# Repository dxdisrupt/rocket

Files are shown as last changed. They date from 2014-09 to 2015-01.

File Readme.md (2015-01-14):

<a name="Title" />
# Compressed Air Rocket and Spark Core Setup #

<a name="overview" />
## Overview ##

The compressed air rocket used here is based on the one presented by Make Magazine in **[How-to: Building a compressed air rocket launcher] (http://makezine.com/2010/07/11/how-to-building-the-compressed-air/)**

You can make your own rockets using a legal sheet of paper, some napkins (to add support to the nose cone), and copious amounts of tape.  Get the template here: [Rocket_Template.pdf](Rocket_Template.pdf?raw=true)

There is an alternate set of instructions for the rocket launcher with more complete instructions on creating the paper rockets here: http://cdn.makezine.com/make/2010/04/compressedairrocket.pdf .  A copy of the PDF is also included in this repository here: [compressedairrocket.pdf](compressedairrocket.pdf?raw=true)

---

<a name="BuildInfo" />
## Build Your Own ##

These docs were originally written to help somebody configure the rocket launcher that was shipped to them.  However, there is only one in existence right now so if you wait to have it shipped to you, you may be waiting a while, and you can't keep it for long.  

Building one is not hard, is great to do with kids or really any group.  

1. Follow the instructions to create your own rocket launcher:
	- [How-to: Building a compressed air rocket launcher] (http://makezine.com/2010/07/11/how-to-building-the-compressed-air/) 
	- Alternate instructions: [compressedairrocket.pdf](compressedairrocket.pdf?raw=true)
	- PDF Template for Paper Rockets: [Rocket_Template.pdf](Rocket_Template.pdf?raw=true)

1. Get a [Spark Core](https://www.spark.io/store) (The one with the chip attenna is fine for most use cases.  If you will be using this outside far away from your WiFi hotspot, you may prefer the one with the ufl connector so you can attach an external antenna for extended range. 

1. Get a Spark Core [Relay Shield](https://www.spark.io/store) 

1. Additional misc parts:

	- Project enclosure for the Spark Relay Sheild, Spark Core, and 9V Battery (I used a sandwich container from the dollar store! High class huh!)

	- Optional On/Off switch for the Spark Core (to help save the battery when you aren't using it)

	- Wire to connect the Spark Core

- An Adventerous attitude is required.  You will likely need to "invent" a few things as you build your own system.  If I get to where I can spec out exact parts and process I will, but then that would take some of the fun out of building your own version. 

---

<a name="inventory" />
## Inventory ##

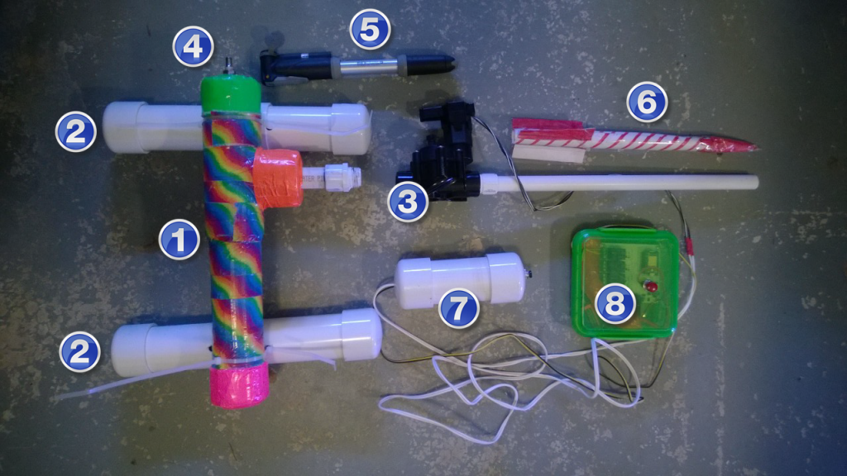
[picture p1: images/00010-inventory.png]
00010-Inventory Inventory


1. Compression Chamber
2. Feet - Attached with Zip Ties
3. Springer Valve and Launch Tube
4. Shrader Valve to charge compression chamber
5. Bike Pump - Attaches to Shrader Valve
6. Paper & Tape Rocket
7. Manual Firing Button & 9v Power Supply
8. Spark Core & Relay Board

The following schematic gives you the basics of the eletronics although the schematic isn't exact.  It was built in [Fritzing](fritizing.org) and there is not current a fritzing part for the Spark IO Relay Shield, so the connections have been approximated here:

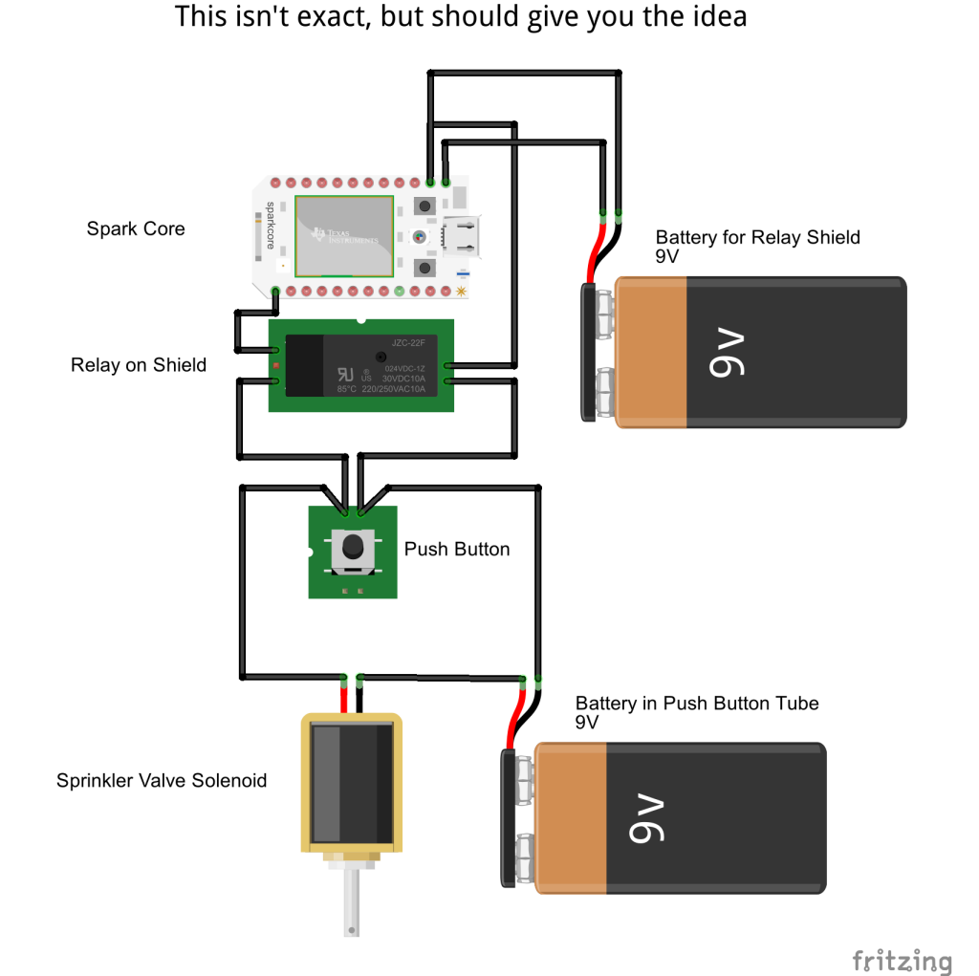
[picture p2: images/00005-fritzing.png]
00005-Fritzing Fritzing


--- 

<a name="tasks" />
## Tasks  ##

1. [Assembling the Rocket Launcher](#Task1)
1. [Installing the Spark Core Windows USB Driver](#Task2)
1. [Installing the Spark-CLI](#Task3)
1. [Configuring WiFi for a Pre-Programmed Spark Core](#Task4)
1. [Flashing the relayWidget Sketch](#Task5)
1. [Identifying your Spark Core](#Task6)
1. [Testing the Spark Core](#Task7)
1. [Using Visual Studio to Create a Launcher Web Site](#Task8)
1. [Publishing your Web Site to Azure](#Task9)

---

<a name="Task1" />
## Assembling the Rocket Launcher ##

1.  Attach the **Sprinkler Valve and Launch Tube** (3) to the **Compression Chamber** (1) using the using the threaded PVC tubing extending from the compression chamber and threading it into the bottom of the sprinkler valve. 

	> **Note:** Be sure that you have it threaded on tightly.  If need be use some plumbers tape to help ensure a good seal.  If the seal here is not good, air will leak out. 

1.  Attach the **Compression Chamber** (1) to the **Feet** (2) using .zip ties.  Tighten the zip ties enough to hold the compression chamber in place, but loose enough that you can still tilt the launch tube for aiming purposes. 

1. **CAREFULLY** remove the cap with the button on it from the **"Manual Firing Button and 9v Power Supply"** by twisting it back and forth while pulling it away from the tube. 

	> **Note:** If you are using my rocket, I just improved the connections inside the tube so you don't have to be AS CAREFUL, but you don't want to the yank the cap off and break the connections.

1. Inside the tube, you should find the 9V Battery and the 9V battery connector.  Connect the battery to the snap connector, then re-insert the battery in the tube and replace the cap. 

	> **Note:** The 9V battery in the push button tube is what actually supplies the power for the sprinkler valve solenoid.  If you make sure to only have the battery connected when you are actively using the rocket, it should last for a very long time.  If you find that the Solenoid does not open when you push the button, you may try replacing the 9V battery in the tube. 

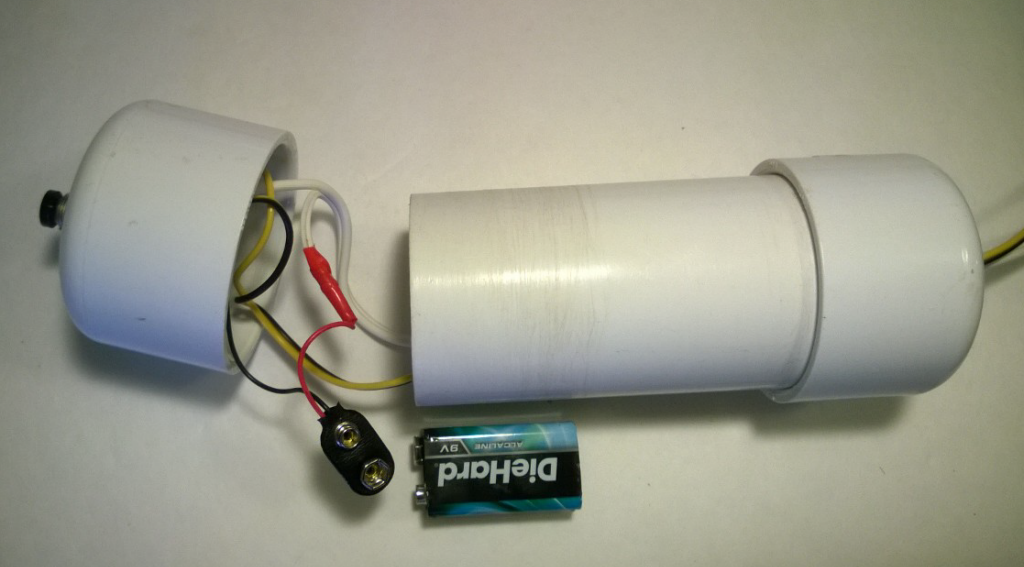
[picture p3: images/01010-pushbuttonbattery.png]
01010-PushButtonBattery Push Button Battery
	

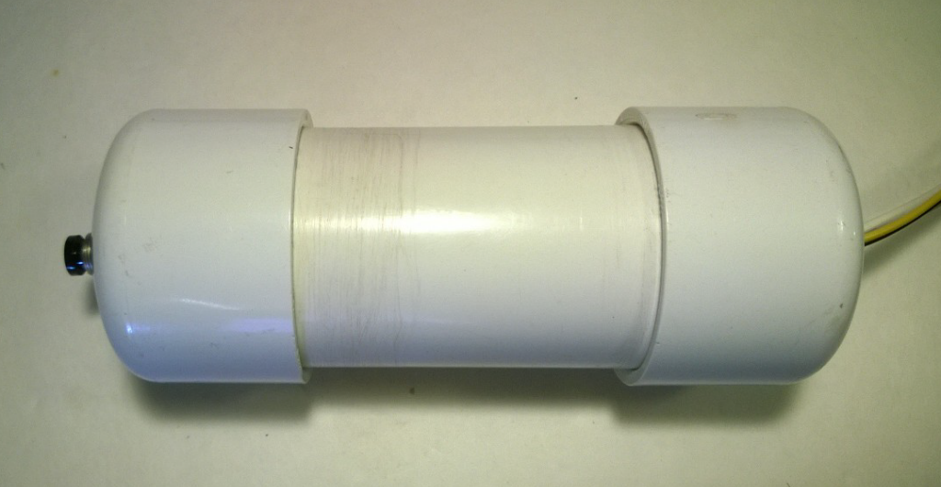
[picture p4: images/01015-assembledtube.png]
01015-AssembledTube Assembled Tube
	

1. I added some disconnects between the sprinkler valve and the manual push button and spark core relay board assemblies.  This makes it easier to disconnect them for shipping.

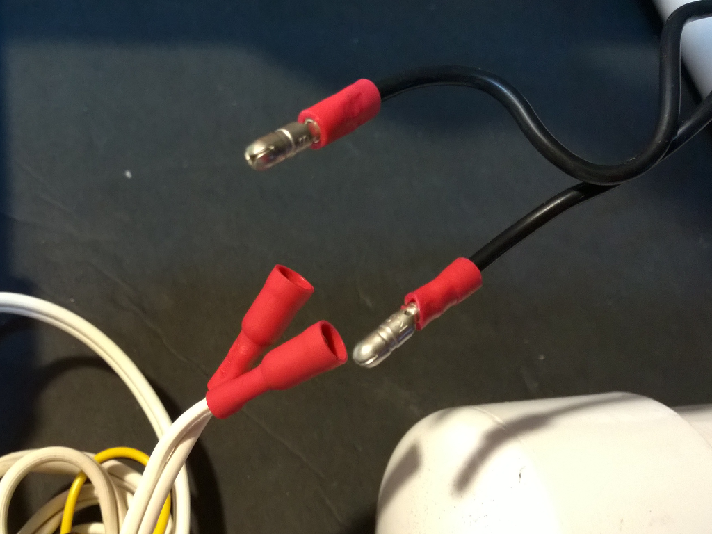
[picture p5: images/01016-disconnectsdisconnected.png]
01016-DisconnectsDisconnected Disconnects Disconnected
	

1. Simply re-connect them if they are disconnected.  ***It doesn't matter which black wire connects to which white wire.  Either way is fine.*** 

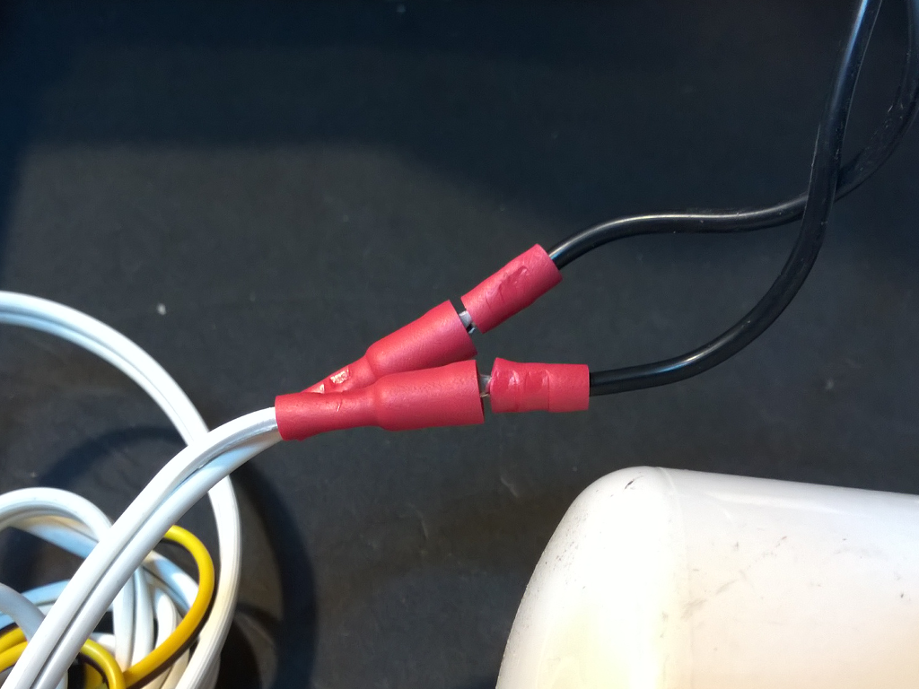
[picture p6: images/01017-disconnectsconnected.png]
01017-DisconnectsConnected Disconnects Connected
	

1. You should now be able to push the pushbutton and hear the solenoid on the sprinkler valve opening and closing (faintly).  If you hold your hand on the solendoid while you repeatedly push the button, you should also be able to feel the solenoid opening and closing. 

1. Attach the **Bike Pump** (5) to the **Shrader Valve** (4).  Again, ensure a good connection. 

1. You can now pump the bycicle pump (just a few times for this initial test): 
	- **WITHOUT A ROCKET** on the launch tube
	- Make sure to **STAY CLEAR OF THE LAUNCH TUBE**

1. **When you know it is safe to do so**, push the manual push button, and verify that air is released from the launch tube.  **Hold the push button down for five seconds to allow all of the air to escape.** 

1. Assuming everything has worked so far, if you have a rocket handy, and you just can't wait, go ahead and **SAFELY** try firing a rocket.  Remember, this is supposed to be a fun thing, not a weapon.  Please **DO NOT EVER AIM THE ROCKET AT SOMEBODY**. I have had MULTIPLE accidental misfires during my use of the rocket, and have been very lucky to have never injured anybody, but this can be dangerous, so please take care. 

	You can aim the rocket by rotating the compression chamber.  If the zip ties are too loose you can tighten them up to add enough friction to keep the compression chamber in place after "aiming"

1. Here is the final assembled rocket launcher:

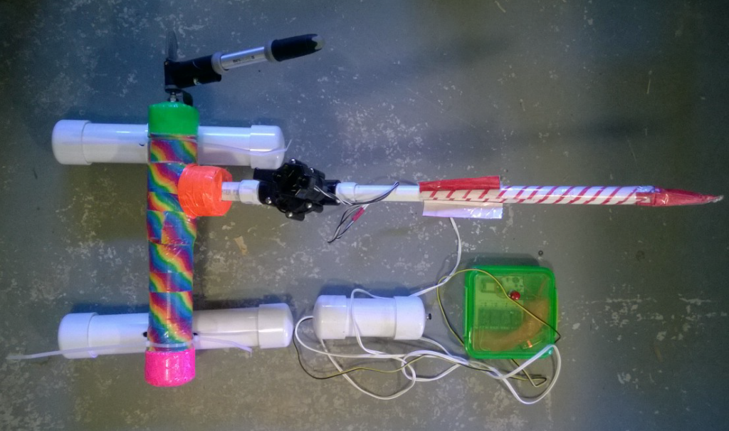
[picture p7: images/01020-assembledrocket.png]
01020-AssembledRocket Assembled Rocket
	

---

<a name="Task2" />
## Installing the Spark Core Windows USB Driver ##

### <span style="color: #090">IF YOU ALREADY HAVE THE WINDOWS USB DRIVER INSTALLED YOU CAN SKIP THIS TASK</span> ###

The steps covered here are specific to configuring a Spark Core using the Command Line Interface on a Windows machine. If you will be working with the spark core from a Mac or Linux box, you can can refer to the [online documentation](http://docs.spark.io/ "Spark.IO Documentation") for configuring a Spark Core. 

1. Before you work with the Spark Core on a Windows Machine, you will need to install the Windows USB Driver.  First, you'll need to download the driver from https://s3.amazonaws.com/spark-website/Spark.zip . Download the .zip file and extract it to a folder on your computer.  

	> **Note:** You can also refer to the documentation for [Connecting to the Spark Core via USB](http://docs.spark.io/connect/#connecting-your-core-connect-over-usb)

1. Connect the Spark Core to your computer via the USB, and ensure that the Spark Core is in **["Listening Mode"](http://docs.spark.io/connect/#connecting-your-core-listening-mode)** by confirming that the RGB LED on the board is flashing blue.  If it isn't, [hold the **"MODE"** button on the Spark Core for about three seconds until it begins flashing](https://vine.co/v/hFHlpBDELeU):

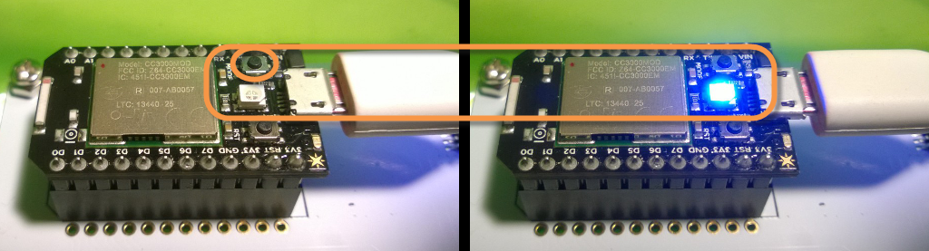
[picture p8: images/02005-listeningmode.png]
02005-ListeningMode Listening Mode
	

1. Open your computer's **"Device Manager"**.  Under **"Other Devices"** you should see the **"Spark Core with WiFi"**.  Right click on the **"Spark Core with WiFi"** and select **"Update Driver Software..."** from the pop-up menu: 

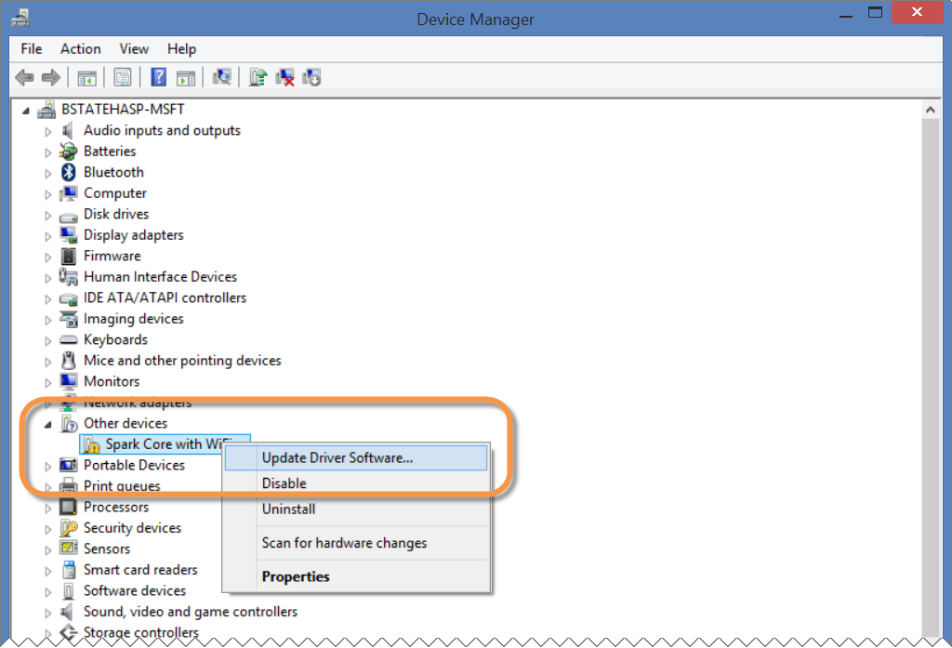
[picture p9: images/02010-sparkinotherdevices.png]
02010-SparkInOtherDevices Spark in Other Devices
	

1. Select the **"Browse my computer for driver software"** option:

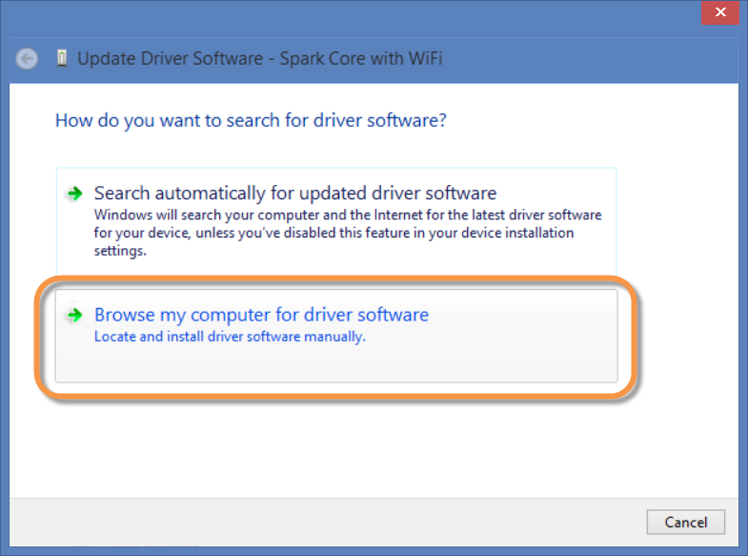
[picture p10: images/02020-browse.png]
02020-Browse Browse
	

1. Then browse to the folder where you extracted the Spark.zip file you downloaded previously with the Windows USB driver.  (There should be a **spark_core.inf** and **spark_core.cat** file in the folder), then click **"Next"**:

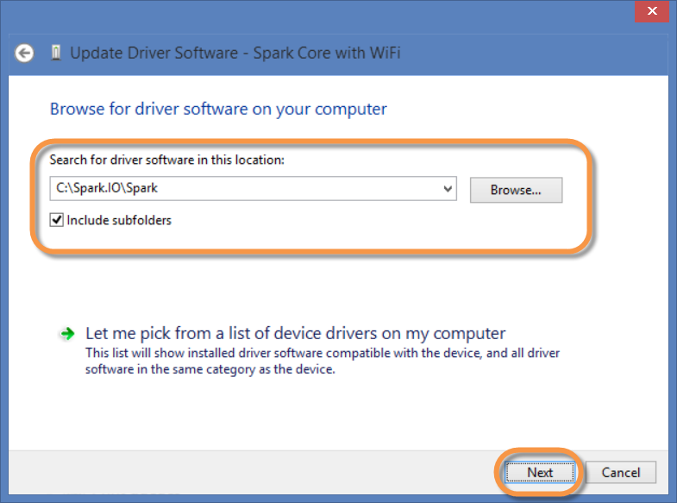
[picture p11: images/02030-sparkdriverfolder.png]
02030-SparkDriverFolder Spark Driver Folder
	

1. In the **"Windows Security"** window, click **"Install"** to install the driver:

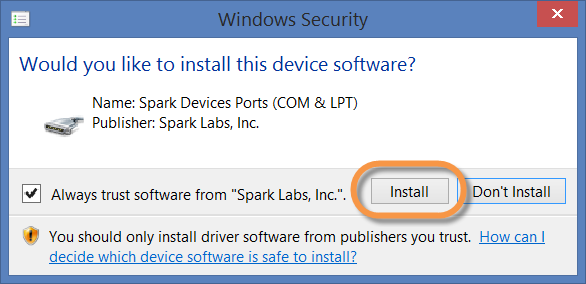
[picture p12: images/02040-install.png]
02040-Install Install
	

1. You should see a confirmation that the **"Spark Core with Wifi and Arduino Compatability"** driver was installed.  Click **"Close"** to close the window. 

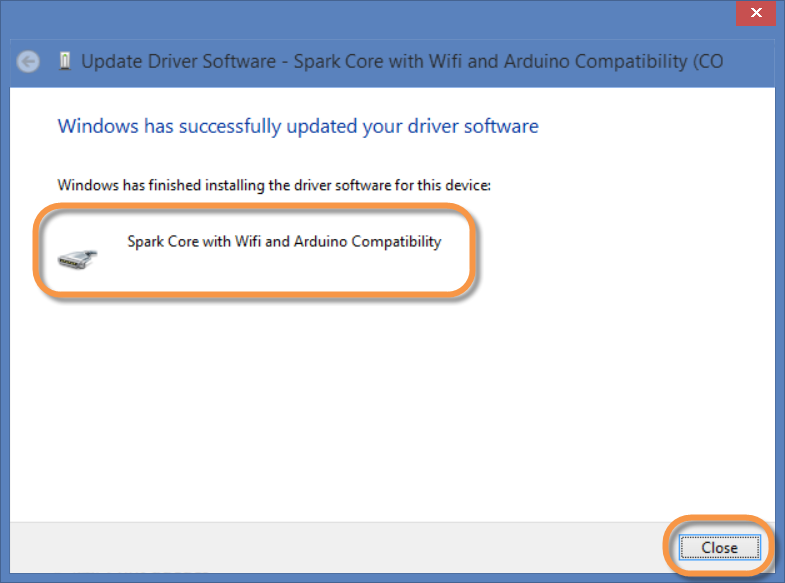
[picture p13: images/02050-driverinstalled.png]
02050-DriverInstalled Driver Installed
	

1. Finally, back in the **"Device Manager"** you should see the Spark Core listed under **"Ports"**:

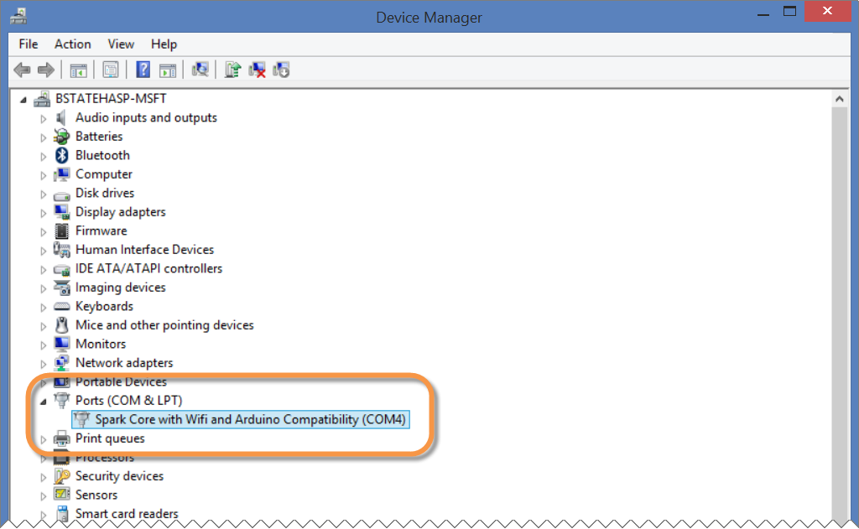
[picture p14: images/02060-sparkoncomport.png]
02060-SparkOnComPort Spark Core on COM Port
	

1. At this point, if you were to use a terminal program (Like [PuTTY](http://www.chiark.greenend.org.uk/~sgtatham/putty/download.html)) you could connect serially to the Spark Core via the COM port listed (COM4 in this case) and issue [some commands](http://docs.spark.io/connect/#connecting-your-core-connect-over-usb).  However, the Spark Command Line Interface (Spark-CLI) offers significantly more functionality, so we'll use that.  

---

<a name="Task3" />
## Installing the Spark-CLI ##

### <span style="color: #090">IF YOU ALREADY HAVE THE LATEST VERSION OF THE SPARK-CLI INSTALLED YOU CAN SKIP THIS TASK</span> ###

The S**park Command Line Interface (Spark-CLI)** is a **Node.js** application that allows you to manage your spark cores, and the code that runs on them.  The Spark-CLI source is available from GitHub at https://github.com/spark/spark-cli and you can read the docs here: http://docs.spark.io/cli/

1.  First, ensure that you have Node.js installed.  You can install it from here: http://nodejs.org/

	> **Note:** It helps if you let the installer install the Node Package Manager (npm) as well as to add Node to the system path.  If you add node the path, you can use node from any Windows Command Prompt. 

1. To install the Spark-CLI using node, you can open a Node.js Command Prompt (or any command administrator prompt if you allowed the Node.js installer to add Node to the path) and issue the following command:

	`npm install -g spark-cli`

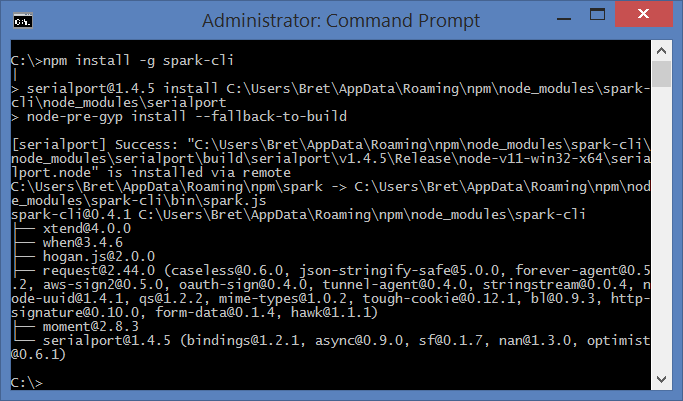
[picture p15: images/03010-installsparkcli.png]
03010-InstallSparkCLI Install Spark-CLI
	

1. This documentation was written with the Spark-CLI version 0.4.1.  If you already have the Spark-CLI installed, you can determine its version using the following command:

	`npm list -g spark-cli`

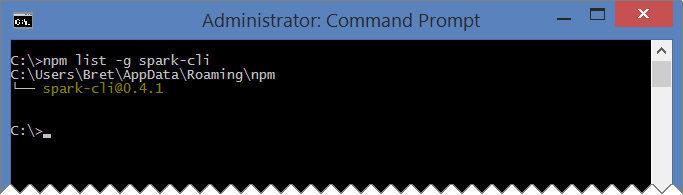
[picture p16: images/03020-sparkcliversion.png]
03020-SparkCliVersion SparkCliVersion
	

1. In addition, you can always upgrade to the latest version of the Spark-CLI using the command: 

	`npm update -g spark-cli`

---

<a name="Task4" />
## Configuring WiFi for a Pre-Programmed Spark Core ##

### <span style="color: #900; font-weight: bold">IF YOU ARE ADDING YOUR OWN SPARK CORE, OR NEED TO RE-PROGRAM AN EXISTING SPARK CORE, SKIP THIS STEP AND GO TO [Flashing the relayWidget Sketch](#Task5)</span> ###

If you received the rocket launcher, with a Spark Core that has been pre-programmed, a Relay Board, and everything already connected, you only need to configure the Spark Core to connect to your local WiFi.

1. Connect the Spark Core to your PC via USB, and place the Spark Core into **"[Listening Mode](http://docs.spark.io/connect/#connecting-your-core-listening-mode)"** by holding down the **"Mode"** button on the spark core until the RGB LED flashes blue repeatedly.

1. Open a Node Command Prompt, and issue the following command 

	`spark setup wifi`

1. Follow the prompts to configure the Spark Core for your WiFi network.  

	> **Note:** Some MiFi wifi hot sports (like my Verizon MiFi), and other networks take the user to a start screen on the first load.  If connecting to your mifi, the Spark might fail to connect the first time.  Try cycling the power on your Spark Core to get it to restart and connect.  If the WiFi network you are connecting to requires a browser based authentication process, you won't be able to connect your Spark Core to it.  You must know the WiFi SSID, Security Mode, and Password.  

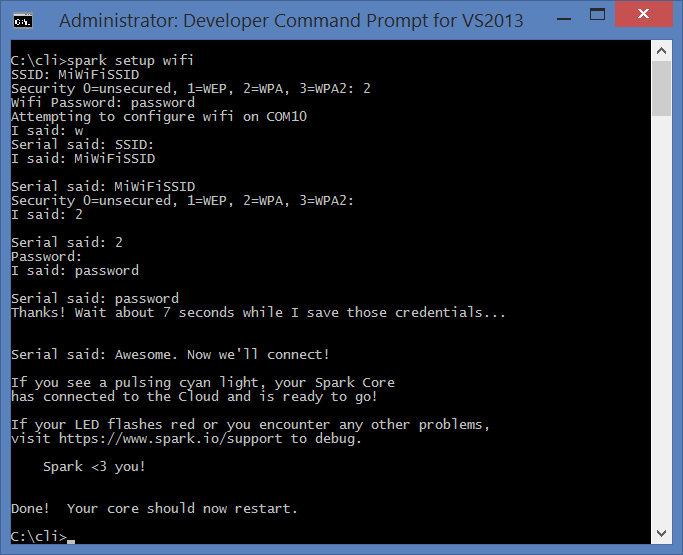
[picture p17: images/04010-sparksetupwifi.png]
04010-SparkSetupWifi spark setup wifi
	

1. When the WiFi setup is complete, you should see the RGB LED on the Spark Core "Breathing Cyan".  This means that [it should have a cyan color (light blue) and should repeatedly fade in and out.](https://vine.co/v/OmOAlMg17Y9) 

---

<a name="Task5" />
## Flashing the relayWidget Sketch ##

### <span style="color: #090; font-weight: bold">If your spark core is already programmed with the relayWidget Sketch, you can skip this step</span> ###

<span style="color: #900; font-weight: bold">If your Spark Core has not been "claimed", you need to do that first.</span> 

<span style="color: #900; font-weight: bold">If the Spark Core you want to claim has already been claimed by another account, you will have to have that account owner remove the core before you can claim it:</span>

`spark core remove <core name / core id>`

<span style="color: #900; font-weight: bold">If your Spark Core is new, or is available to be claimed you can use the Spark-CLI commands:</span>

```
spark cloud login
spark setup
```

<span style="color: #900; font-weight: bold">You can find the instructions for connecting and claiming a core here: http://docs.spark.io/connect/</span>

The **"relayWidget"** sketch (app) we use below is used to drive a Spark Core that is connected to a Spark [Relay Shield](http://docs.spark.io/shields/#relay-shield).  The relay shield makes it simple for a single Spark Core to control up to four other circuits.  In our case, with the rocket, we only need a single circuit.  We'll use the first relay (connected to digital pin D0) to override the manual push-button switch on our compressed air rocket.  We connect the **"Common"** (COMM) and **"Normaly Open"** (NO) ports on the first relay accross the swtich.  Then we we use the Spark Core to drive the pin (D0) HIGH, it "closes" the switch, which supplies the voltage to the solenoid on the Sprinkler Valve and launches the rocket.  Cool! 

Our relayWidget sketch publishes a single function called **"cycleRelay"** via the Spark cloud.  The **"cycleRelay"** function is used to toggle the state of a relay, pause for a given time, then toggle it back.  We'll use that to turn the relay "on" for a time, then back off (so it is ready to fire again).  The cycleRelay takes a single string argument in the form of "r#,delay" where "#" is the relay number (1,2,3,4), and "delay" is the number of milliseconds to wait before toggeling the state back.  We want to send a "command" string of "r1,5000" to toggle the state first relay on (really D0), wait for five seconds, then toggle it back off. 

You could use this sketch to control anything connected to the relay board, and you could publish other functions that turn relays on or off specifically, rather than just cycling them from off to on and back off again. 

1. Login to the [Spark Build](https://www.spark.io/login) web development environment with your Spark.IO credentials (the same credentials you used to claim your Spark Core): https://www.spark.io/login 

1. If this isn't your first sketch, click the **"CREATE NEW APP"** button:

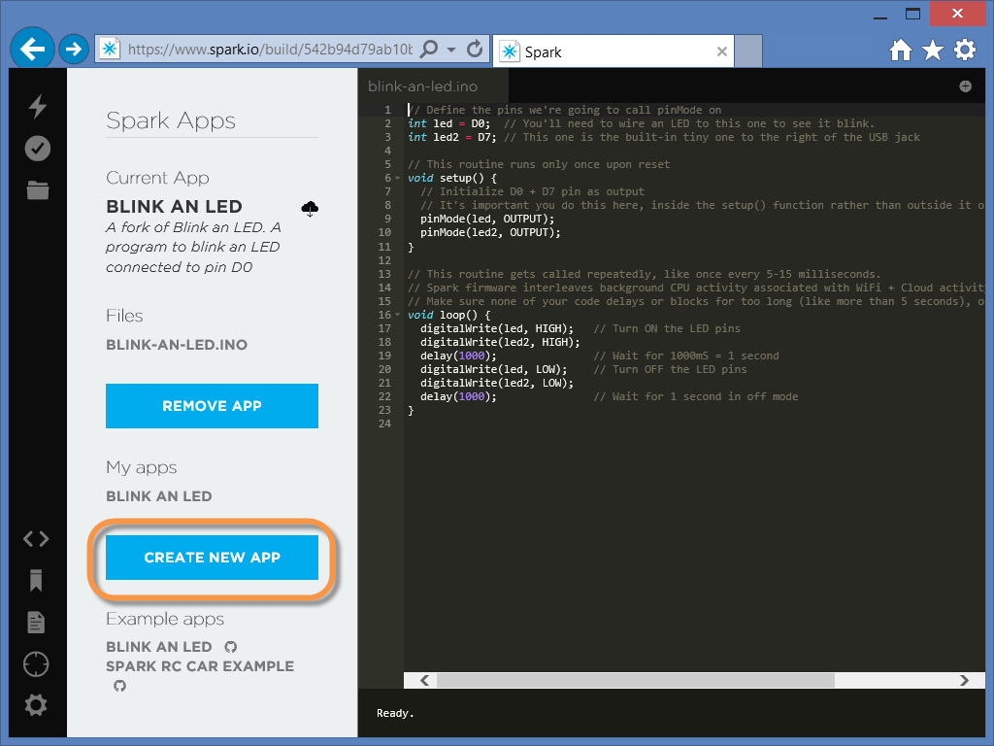
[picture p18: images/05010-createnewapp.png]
05010-CreateNewApp Create New App Button
	

1. When prompted, enter **"relayWidget"** as the name for your new app:

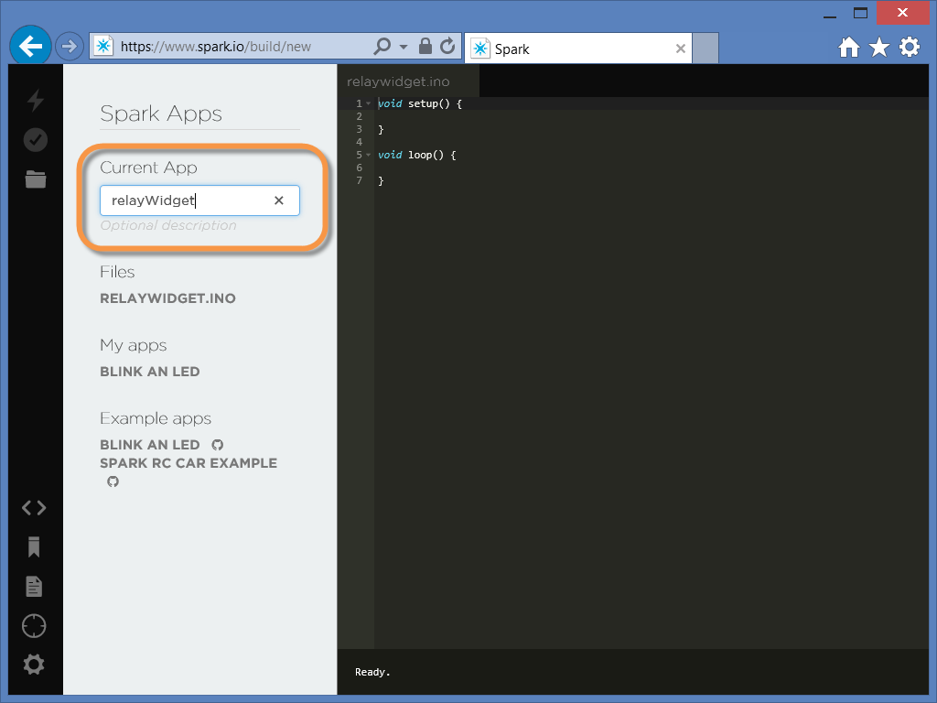
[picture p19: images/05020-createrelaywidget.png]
05020-CreateRelayWidget Create relayWidget app
	

	> **Note:** You can also get this code from the [relayWidget.ino](./relayWidget/relayWidget.ino) code file

	> **Note:** although the sketch has a **.ino** extension, you ***can't compile and deploy*** this to the Spark Core using the Arduino IDE.  You need to use either the Spark web interface, or the [Spark-CLI](http://docs.spark.io/cli) to compile and flash this code onto your Spark Core.  

1. Paste the following code into the code window:

	````C++
	int relayPin[4] = {D0,D1,D2,D3};
	int builtinLed = D7;

	int relayState[4] = {LOW,LOW,LOW,LOW};

	void setup()
	{
		//Initilize the relay control pins as output, and their state
		for(int r = 0; r <= 3; r++)
		{
			 pinMode(relayPin[r], OUTPUT);
			 digitalWrite(relayPin[r],relayState[r]);
		}
		
		//Setup the builtinLed for output
		pinMode(builtinLed,OUTPUT);
		//and make sure it is off...
		digitalWrite(builtinLed, LOW);

		//register the cycle relay function
		Spark.function("cycleRelay", cycleRelay);
		
		Serial.begin(9600);
	}

	void loop()
	{
		// This loops for ever
	}

	int cycleRelay(String command)
	{
		 Serial.print("command: ");
		 Serial.println(command);    
		 //parse the relay number, minus 1 because pin #s start at 0
		 int relayNumber = command.charAt(1) - '0' - 1;
		 //do a sanity check, if we didn't get a good number, exit
		 if(relayNumber < 0 || relayNumber > 3) {
			Serial.print("Relay # not good:");
			Serial.println(relayNumber);
			return -1;
		 }
		 
		 Serial.print("Relay Number: ");
		 Serial.println(relayNumber);
		 
		 //next, get the delay, if none, default to 100ms
		 int pause=100;
		 int comma = command.indexOf(',');
		 if(comma > -1) {
			String pauseString = command.substring(comma+1, command.length());
			Serial.print("pauseString: ");
			Serial.println(pauseString);
			pause = pauseString.toInt(); 
		 }

		 Serial.print("comma: ");
		 Serial.print(comma);
		 Serial.print(" relay: ");
		 Serial.print(relayNumber);
		 Serial.print(" delay: ");
		 Serial.println(pause);
		 
		 toggleRelay(relayNumber);
		 delay(pause);
		 toggleRelay(relayNumber);

		 return 1;
	}

	void toggleRelay(int relay) {
		 relayState[relay] = (relayState[relay] == HIGH) ? LOW : HIGH;
		 digitalWrite(relayPin[relay],relayState[relay]);
		 //Toggle the builtin LED on the board as well
		 //This is just to help somebody test their Spark Core
		 //if it isn't currently connected to a Relay Board
		 digitalWrite(builtinLed,relayState[relay]);
	}
	````

1. Click the **"Save"** button (looks like a folder, dont' ask me why) to save the sketch:

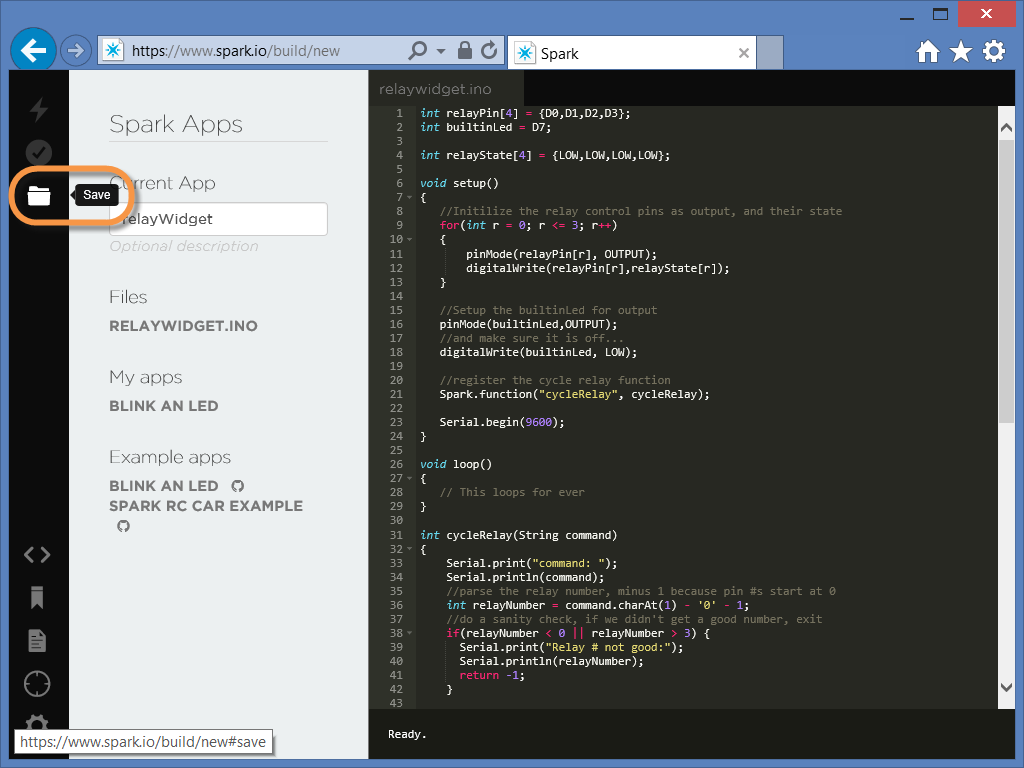
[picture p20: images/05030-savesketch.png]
05030-SaveSketch Save Sketch
	

1. You can then **"Verify"** your sketch:

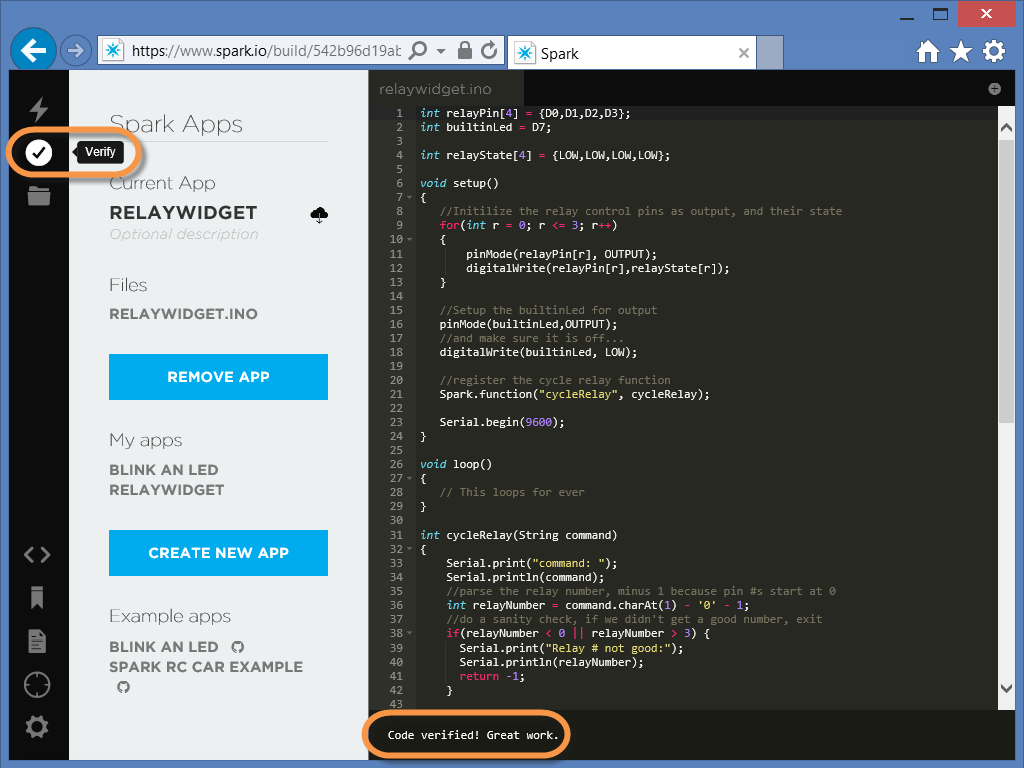
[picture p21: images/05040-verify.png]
05040-Verify Verify Code
	

1. If you have claimed multiple cores with your account, make sure that the correct Spark Core is set as the target, by choosing the **"Cores"** option along the left, then clicking on the **"Star"** icon next to the core you want to flash: 

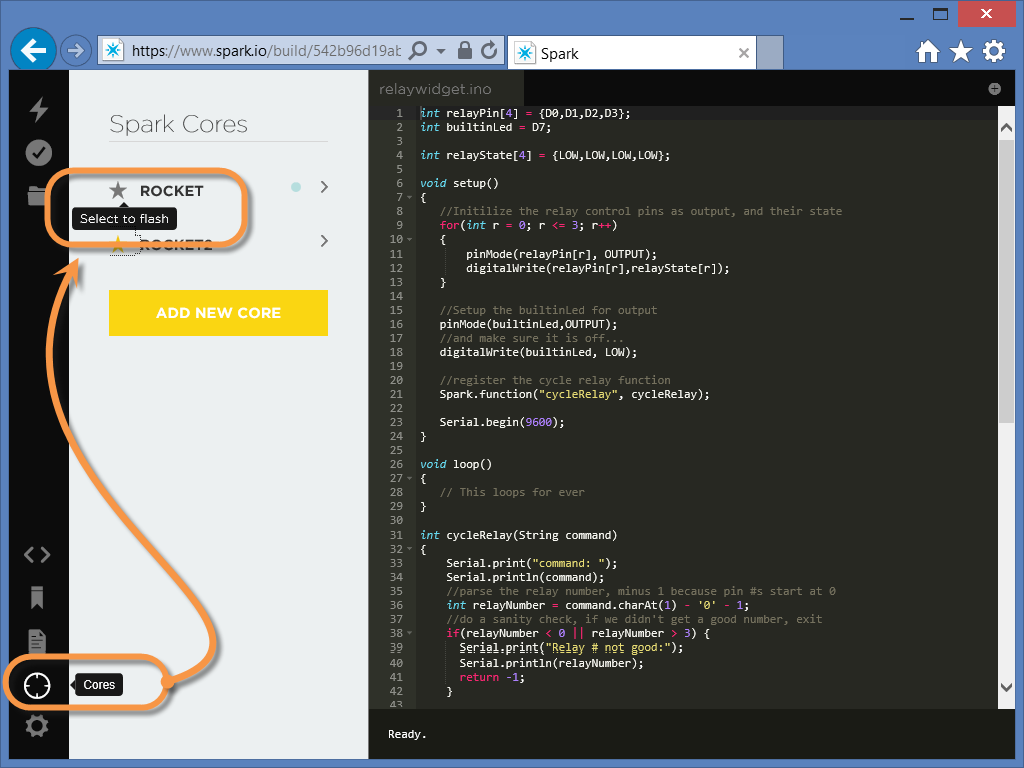
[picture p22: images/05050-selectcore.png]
05050-SelectCore Select Core
	

1. Finally, you can flash the code to your core: 

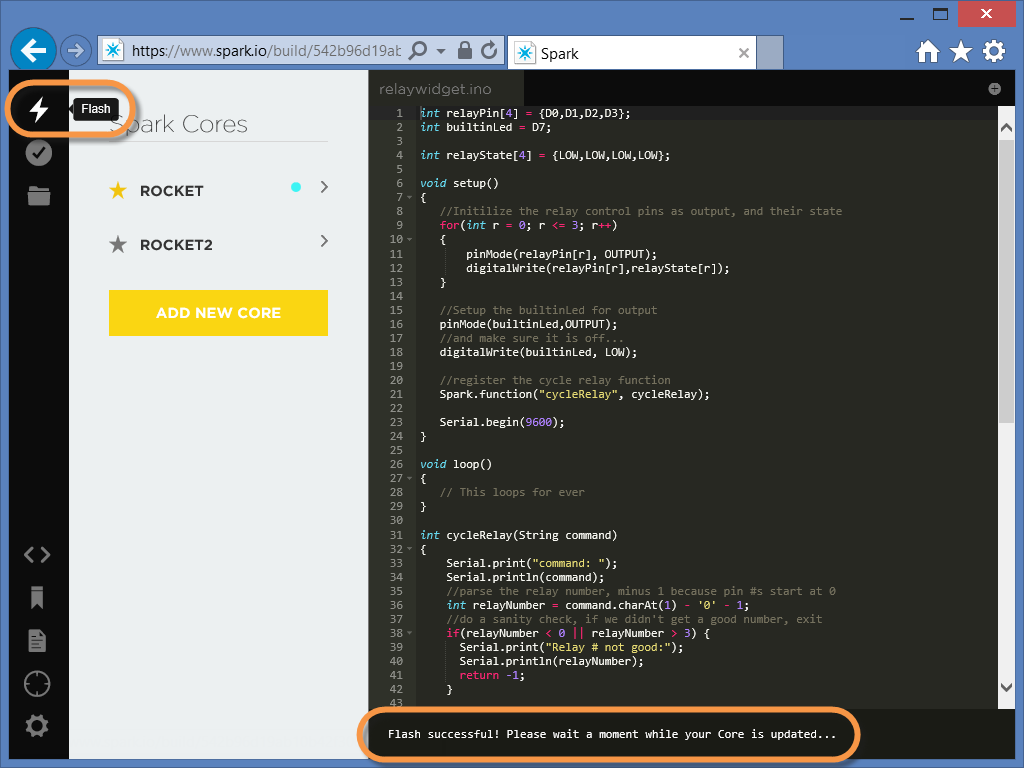
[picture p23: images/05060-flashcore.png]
05060-FlashCore Flash Core
	

1. You know your core is ready when it is once again "[breathing cyan](https://vine.co/v/OmOAlMg17Y9)".

---

<a name="Task6" />
## Identifying your Spark Core ##

<span style="color: #900; font-weight: bold">If the Spark Caore you are using has been claimed by another account, you will need that account owner to supply you with your device's Core ID and Access Token</span>

Before you can call the cycleRelay function on your Spark Core, you need to know 

- The Spark Core's Core ID
- The Access Token for your account

We'll walk through finding both of those here.

1. You can determine your Spark Core's Core ID using the Spark-CLI if it is connected to your PC and "breathing cyan" by issuing the following commands: 

	```
	spark cloud login
	spark cloud list
	```

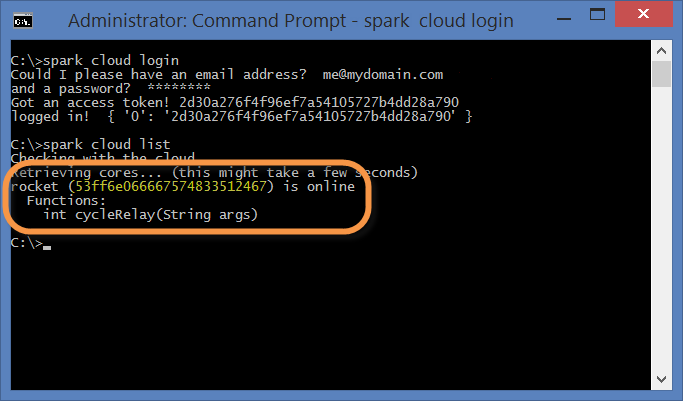
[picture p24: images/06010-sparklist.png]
06010-SparkList Spark List
	

1. You can also determine your Spark Core's ID from the [Spark Build](https://www.spark.io/login) web interface.  Login to [Spark Build](https://www.spark.io/login), and from the **"Cores"** page, click on the arrow next to your core to see it's Core ID:

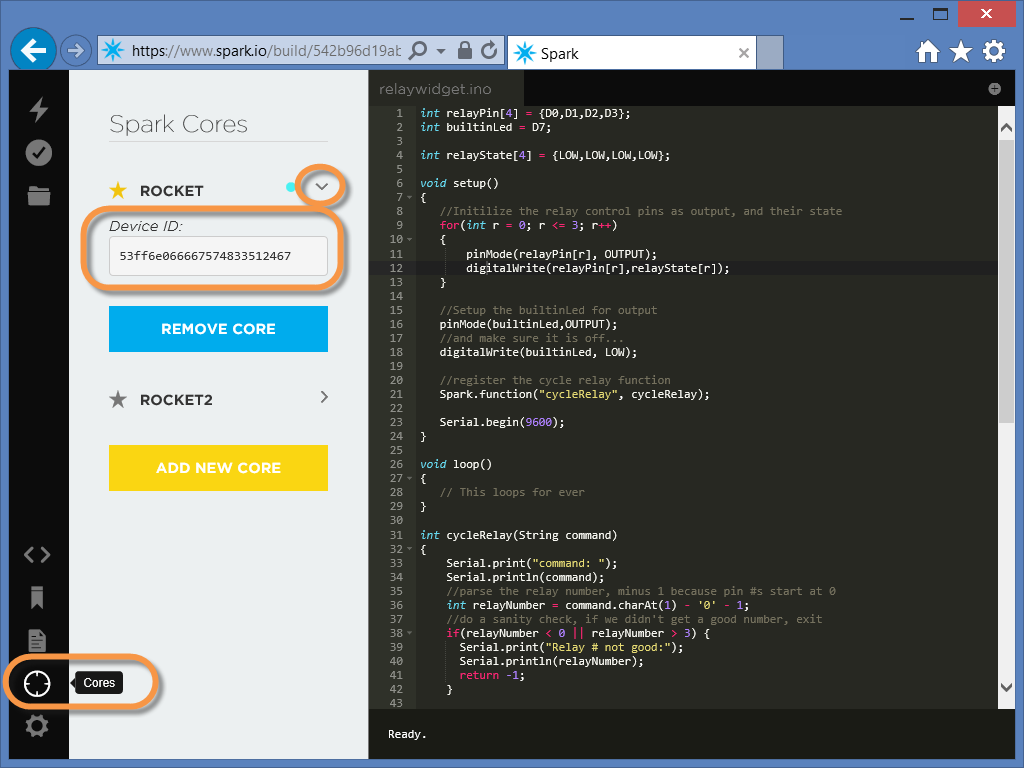
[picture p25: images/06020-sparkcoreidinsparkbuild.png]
06020-SparkCoreIDInSparkBuild Spark Core Device ID in Spark Build
	

1. Your access token can also be retrieved from the Spark Build web interface.  Click on the **"Settings"** link, and copy your Access Token from there: 

	> **Note:** Access Tokens expire every 90 days, so you will need to occasionally update the Access Token in your client.  You can learn more about access tokens here: http://docs.spark.io/api/#spark-cloud-api-authentication

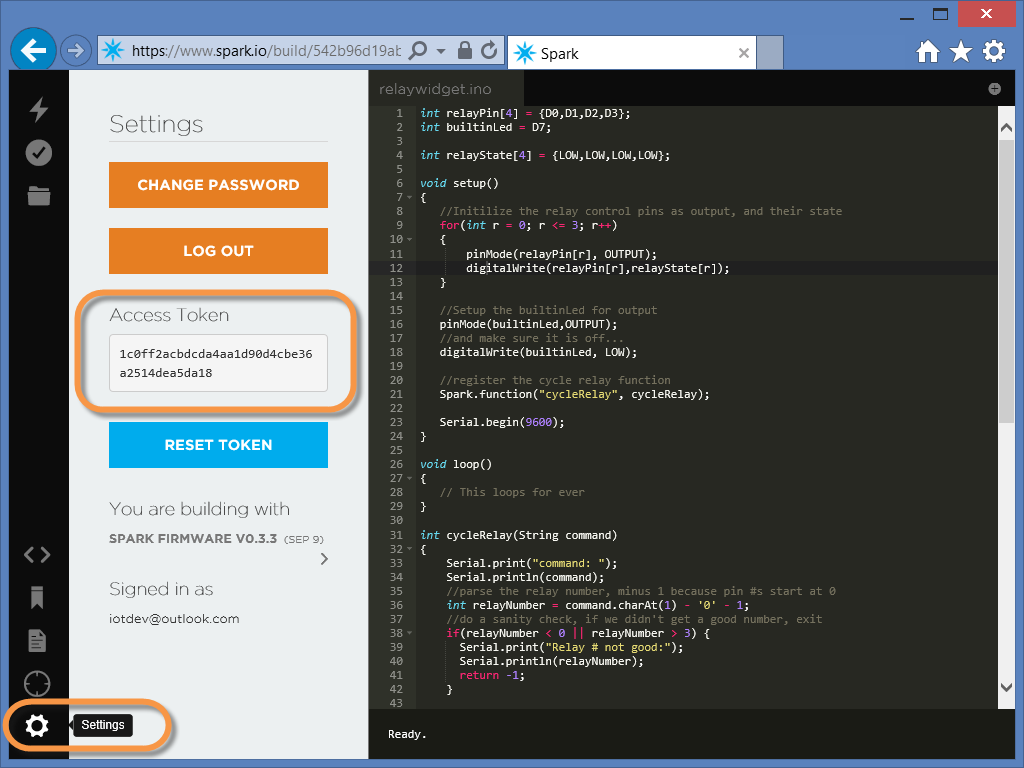
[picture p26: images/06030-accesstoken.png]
06030-AccessToken Access Token
	
---

<a name="Task7" />
## Testing the Spark Core ##

Ok, if you got this far it is assumed that you have a Spark Core connected to a Relay Sheild that is properly wired into the compressed air rocket launcher. You can now disconnect the Spark Core from your computer (disconnect the USB cable), and power it instead from a 9V battery connected to the Relay Shield.  

We will be using the [Spark REST api](http://docs.spark.io/api) to call the **"cycleRelay"** function published by the **"relayWidget"** app we flashed onto the Spark Core.  

The REST API requires that all reqests include the **"Access Token"** for the account that the spark belongs to, as well as the Spark Core's device ID.  Use the instructions in the [Identifying your Spark Core](#Task6) section to retrieve those values if needed. 

Cycle relay takes a single **"command"** string argument in the form of:

`r#,<delay>`

where `#` is the relay number (1-4) and `<delay>` is the number of milliseconds to pause between relay states.  

For example, the following command string toggles relay 1 (`r1`) from off to on, pauses for five seconds (`5000` ms) then toggles the relay state from on back to off:

`r1,5000`

You can call the **"cycleRelay"** function on the spark a number of ways:

- Spark-CLI
- Curl
- A REST Client Tool
- A custom app

We will cover the first three here, and leave the custom app implementation up to you.

1. Connect the 9V battery to the snap connector in the Spark / Relay Shield Box, then turn on the power switch to power the Spark and the Relay Shield:

	> **Note:** This battery powers just the Spark Core and the Relays on the Relay Shield.  The 9V battery in the manual push-button tube is still needed to power the solenoid on the Sprinker Valve.  As before, if you keep this battery connected only when you are actually using the Rocket, the battery should last a long time.  However, be prepared to replace the battery if needed. 

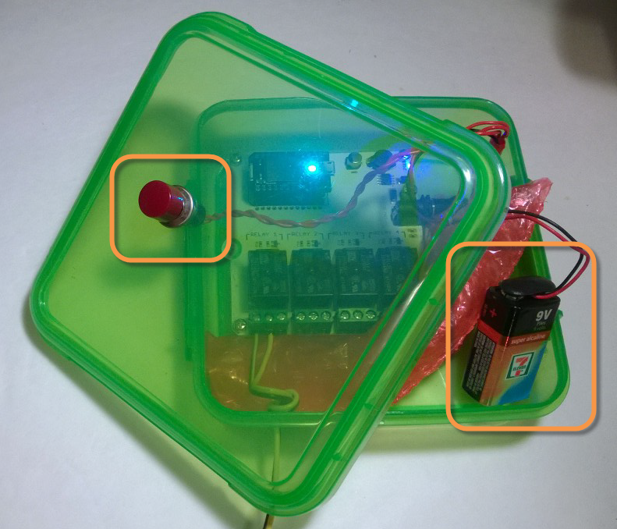
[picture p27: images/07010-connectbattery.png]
07010-ConnectBattery Connect Battery
	

1. When testing the **"cycleRelay"** function, there are two ways you can tell if it is working:

	- If the little LED next to the USB port on the Spark Core turns blue.  This mimicks the relay state and allows you to test the app even if the Spark Core isn't connected to the Relay Shield

	- The LED above the corresponding relay on the relay shield lights up when the relay is activated.  

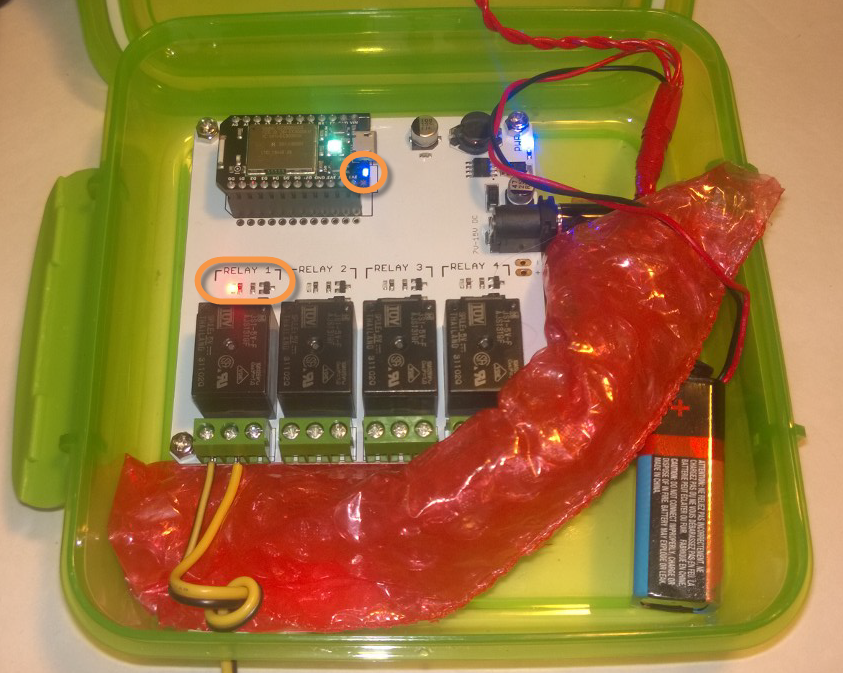
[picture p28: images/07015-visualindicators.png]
07015-VisualIndicators Visual Indicators
	

1. To use the Spark-CLI to call the cycleRelay function on your Spark Core first make sure you are logged in via the Spark CLI:

	`spark cloud login`

	Then run either:

	`spark call <deviceid> cycleRelay r1,5000`

	or 

	`spark call <core name> cycleRelay r1,5000`

	for example:

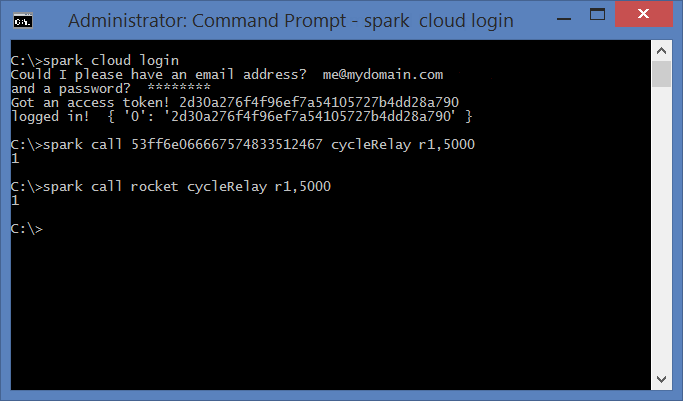
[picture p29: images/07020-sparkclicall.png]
07020-SparkCLICall Spark-CLI Calls
	

	> **Note:** you can change the `r1,5000` parameters to toggle a different relay for a different duration

1. You can also use [curl](http://curl.haxx.se/download.html) to test your spark using the following format:

	`curl https://api.spark.io/v1/devices/<core id>/cycleRelay -k -d access_token=<access token> -d params=r1,5000`

	For example:

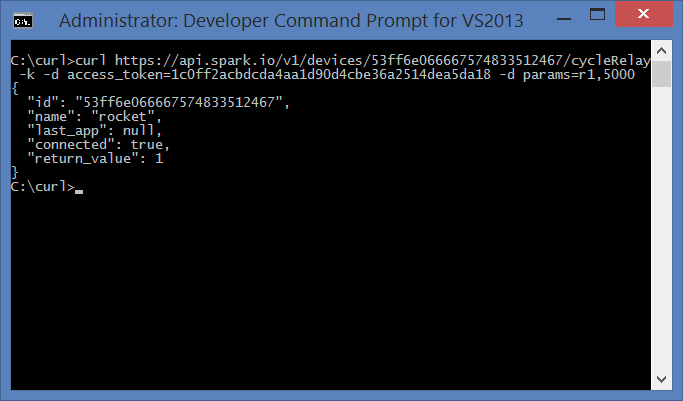
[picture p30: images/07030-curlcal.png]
07030-CurlCall Curl Call
	

	> **Note:** Again, you can modify the `r1,5000' value above to cycle a different relay for a different duration

1. You can also use a REST test client like the ["Advanced Rest Client" app for Chrome](http://chromerestclient.appspot.com/)

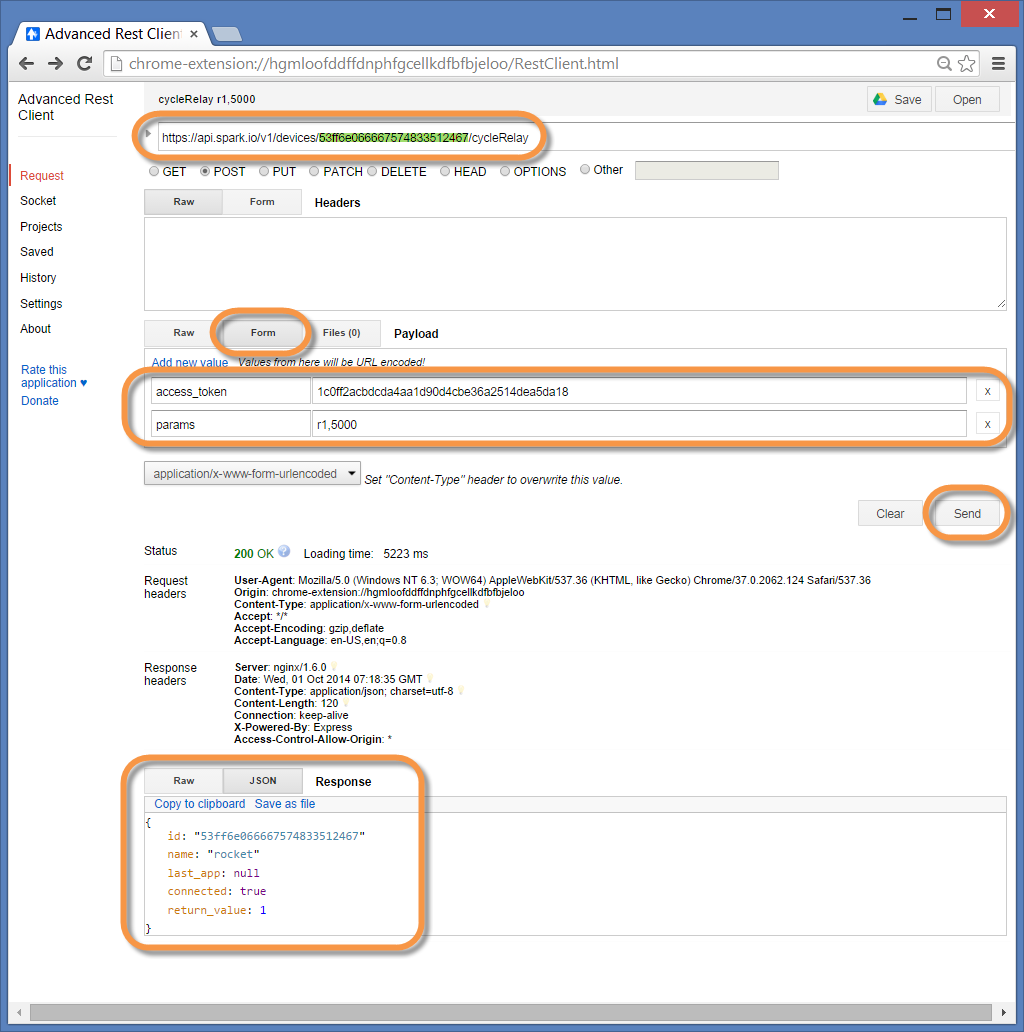
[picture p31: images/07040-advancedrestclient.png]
07040-AdvancedRestClient Advanced REST Client
	

1. To create a custom app (A Windows or Windows Phone App, Web App, iOS, Android, etc) you can read up on the [Spark REST api](http://docs.spark.io/api) and implement your client code accordingly.

1. Once you have a test working reliably, you can now SAFELY charge the compression chamber with the bike pump, place a rocket on the launcher and go for it! 
	
	<span style="color: #900; font-weight: bold">Be careful not to over pressurize the chamber.  For an "indoor" demo you want relatively low pressure.  Outdoors, you can increase it.  Start low, test, and increase as needed.</span>

---

<a name="Task8" />
# Using Visual Studio to Create a Launcher Web Site #

Now that you know that you can launch the rocket using the REST API, you can really write any kind of app you want to launch the rocket.  It could be a phone app, a desktop app, a web site, whatever. In this step, we'll create a simple web site (really, just a web page) using **Visual Studio Community Edition**.  

1. If you don't have Visual Studio Community Edition, you can get a copy from [visualstudio.com](http://visualstudio.com).  You can also use Visual Studio Express for Web 2013, or another full version of Visual Studio 2013 if you already have them.  Make sure to also install the latest Azure SDK from http://azure.microsoft.com/en-us/downloads/ . We'll assume you are using Visual Studio 2013 Community Edition. 

1. In the Visual Studio window, from the menu bar, select **"File"** | **"New"** | **"Web Site..."** :

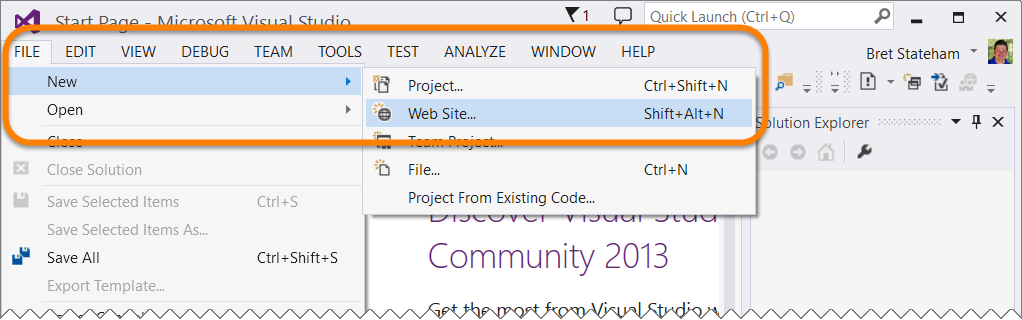
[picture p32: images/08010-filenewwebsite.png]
08010-FileNewWebSite File New Web Site
	

1. Then, in the **"New Web Site"** window, select **"Visual C#"**, **"ASP.NET Empty Web Site"**, and then specify the file system path to the folder where you want to create the web site:

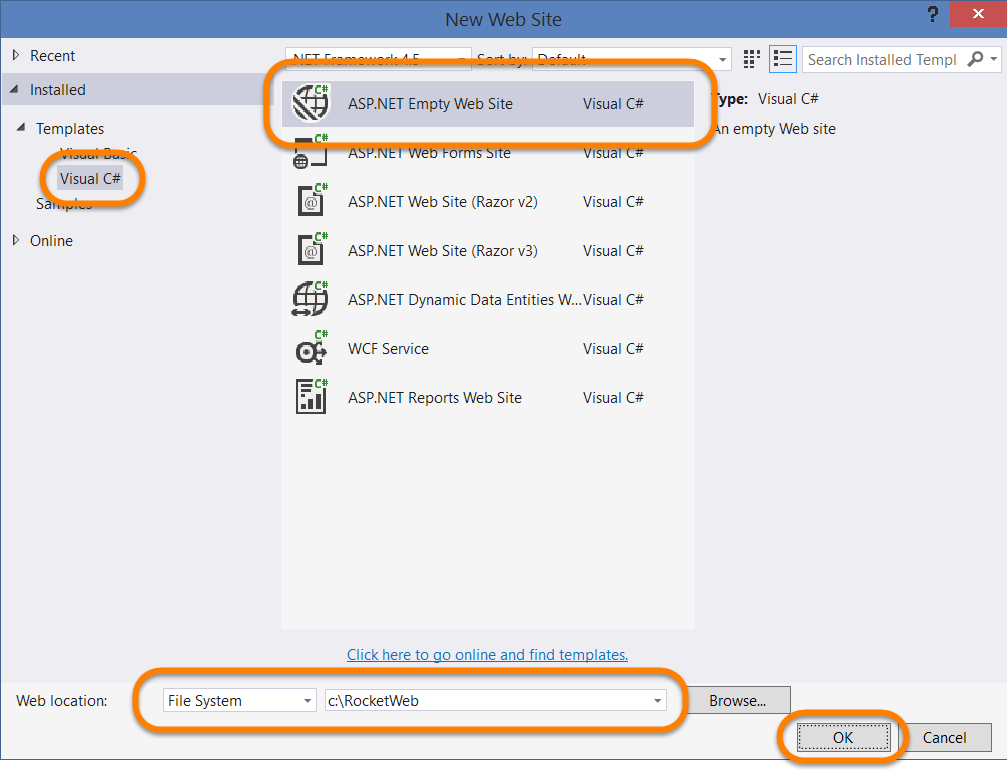
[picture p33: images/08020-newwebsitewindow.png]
08020-NewWebSiteWindow New Web Site Window
	

1. In the Visual Studio **"Solution Explorer"** window, right click on the name of your web site, and select **"Add"** | **"Add New Item..."** from the pop-up menu:

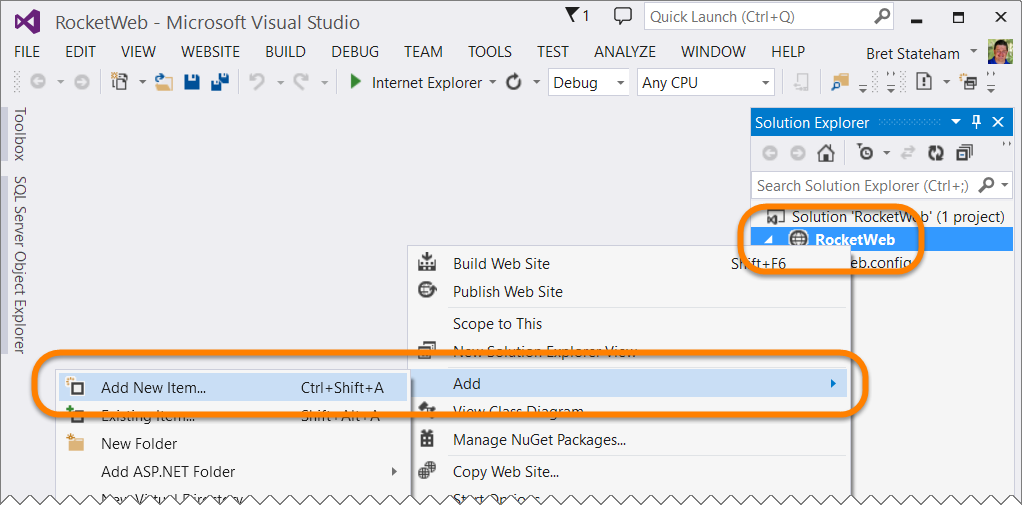
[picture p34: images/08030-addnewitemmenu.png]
08030-AddNewItemMenu Add New Item Menu
	

1. In the **"Add New Item"** window, select **"HTML Page"**, then give the file the name **"index.html"** and click **"Add"**:

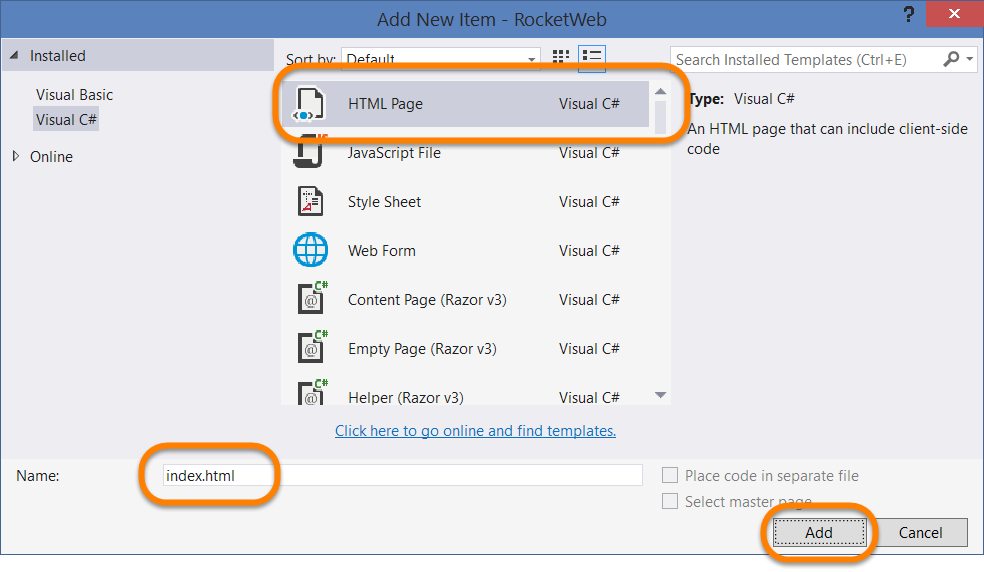
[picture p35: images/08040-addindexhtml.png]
08040-AddIndexHtml Add index.html
	

1. Replace the entire contents of the new index.html file with the following code:

	> **Note:** You can also copy the contents from the [RocketWeb/index.html](./RocketWeb/index.html) file

	````HTML
	<!DOCTYPE html>
	<html lang="en">
	<head>
	  <meta charset="utf-8">
	  <meta http-equiv="X-UA-Compatible" content="IE=edge">
	  <meta name="viewport" content="width=device-width, initial-scale=1">
	  <meta name="description" content="">
	  <meta name="author" content="">
	  <link rel="icon" href="../../favicon.ico">

	  <title>Rocket Launcher</title>

	  <!-- Bootstrap core CSS --><!-- Latest compiled and minified CSS -->
	  <link rel="stylesheet" href="https://maxcdn.bootstrapcdn.com/bootstrap/3.3.1/css/bootstrap.min.css">
	  <!-- Bootstrap theme --><!-- Optional theme -->
	  <link rel="stylesheet" href="https://maxcdn.bootstrapcdn.com/bootstrap/3.3.1/css/bootstrap-theme.min.css">

	  <!-- HTML5 shim and Respond.js for IE8 support of HTML5 elements and media queries -->
	  <!--[if lt IE 9]>
		 <script src="https://oss.maxcdn.com/html5shiv/3.7.2/html5shiv.min.js"></script>
		 <script src="https://oss.maxcdn.com/respond/1.4.2/respond.min.js"></script>
	  <![endif]-->

	  <style type="text/css">
		 /* start the alerts out as hidden */
		 .alert {
			display: none;
		 }
	  </style>
	</head>

	<body role="document">

	  <div class="container theme-showcase" role="main">

		 <!-- Main jumbotron for a primary marketing message or call to action -->
		 <div class="jumbotron">
			<h1>Rocket Launcher</h1>
			<p>
			  Use this page to launch your rocket!  Refer to the documentation at <a href="http://github.com/dxdisrupt/rocket" target="_blank">http://github.com/dxdisrupt/rocket</a> for more information!
			</p>
			<p>
			  <a class="btn btn-primary btn-lg" role="button" href="http://github.com/dxdisrupt/rocket" target="_blank">Learn more &raquo;</a>
			</p>
		 </div>

		 <!-- This is the Launch button.  We'll click this to launch the rocket.
				It's click event handler get's wired up in the document.onready
				function below -->
		 <p>
			<button id="buttonLaunch" type="button" class="btn btn-block btn-lg btn-danger">LAUNCH</button>
		 </p>

		 <!-- These divs are used to give feed back to the user while the rocket is launching or 
				based on the success or failure of the launch  -->
		 <div id="alertInfo" class="alert alert-info" role="alert">
			<strong>LAUNCHING ROCKET!</strong> This will take about five seconds if everything works right, or up to thirty seconds if there is a problem. Please wait....
		 </div>

		 <div id="alertSuccess" class="alert alert-success" role="alert">
			<strong>CONGRATULATIONS!</strong>: Your rocket should be flying high!
		 </div>

		 <div id="alertFailure" class="alert alert-danger" role="alert">
			<strong>EPIC FAIL!</strong>: Something went wrong.  Make sure that you updated the Spark Core ID and Access Token in the source code, and that the Spark Core is on and breathing cyan.
		 </div>

	  </div> <!-- /container -->
	  <!-- Bootstrap core JavaScript
	  ================================================== -->
	  <!-- Placed at the end of the document so the pages load faster -->
	  <script src="https://ajax.googleapis.com/ajax/libs/jquery/1.11.1/jquery.min.js"></script>
	  <!-- Latest compiled and minified JavaScript -->
	  <script src="https://maxcdn.bootstrapcdn.com/bootstrap/3.3.1/js/bootstrap.min.js"></script>
	  <script src="../../assets/js/docs.min.js"></script>
	  <!-- IE10 viewport hack for Surface/desktop Windows 8 bug -->
	  <script src="https://maxcdn.bootstrapcdn.com/bootstrap/3.3.1/js/ie10-viewport-bug-workaround.min.js"></script>

	  <script>

		 $(document).ready(function () {
			//wire up the button click event handler
			$('#buttonLaunch').click(function () {
			  //When the user clicks the button, call the launch method (defined below)
			  launch();
			});
		 });

		 //This function uses jQuery's ajax functionality to call the Spark Core REST API
		 //and launch the rocket. Make sure to update the coreId and accessToken variables
		 //with your values...
		 launch = function () {
			
			/*
			!!!!!!!!!!!!!!!!!!!! IMPORTANT !!!!!!!!!!!!!!!!!!!!

			You need to update the coreId and accessToken variables with your Spark Core's 
			Core ID and your account's Access Token. Refer to the following link if you 
			need help finding those values: 
			https://github.com/dxdisrupt/rocket#Task6
			*/
			var coreId = "PUT YOUR CORE ID HERE";
			var accessToken = "PUT YOUR ACCESS TOKEN HERE";

			//This builds the URL to the REST API endpoint for the cycleRelay function 
			//with your given coreId
			var url = "https://api.spark.io/v1/devices/" + coreId + "/cycleRelay";

			//Turn on the alertInfo div to show the user that the rocket launch is being attempted
			showAlerts("info");

			//Make the Ajax Call
			$.ajax({
			  type: "POST",
			  url: url,
			  data: {
				 access_token: accessToken,
				 args: "r1,5000" //Fires relay 1 for 5 seconds to make sure all the air exits the launcher
			  },
			  complete: function (jqxhr, status) {
				 //Figure out if the call was successful or not
				 //The cycleRelay function should return a value of 1 if all was well
				 //If we got anything else back, it failed. Use that knowledge to show
				 //the appropriate alert div.
				 var success = false;
				 if (jqxhr.responseJSON.return_value === 1) {
					showAlerts("success");
				 } else {
					showAlerts("failure");
				 }
			  }
			});
		 };

		 //This uses the state argument values "info","success","failure" or "none"
		 //to determine which of the alert divs (if any) to hide or show.
		 showAlerts = function (state) {
			switch (state) {
			  case "info":
				 $('#alertInfo').show();
				 $('#alertSuccess').hide();
				 $('#alertFailure').hide();
				 break;
			  case "success":
				 $('#alertInfo').hide();
				 $('#alertSuccess').show();
				 $('#alertFailure').hide();
				 break;
			  case "failure":
				 $('#alertInfo').hide();
				 $('#alertSuccess').hide();
				 $('#alertFailure').show();
				 break;
			  case "none":
			  default:
				 $('#alertInfo').hide();
				 $('#alertSuccess').hide();
				 $('#alertFailure').hide();
				 break;
			}
		 };

	  </script>
	</body>
	</html>
	````

1. Next, you need to replace some code in the file. On lines 102 and 103 (or thereabouts), you need to update the `coreId` and `accessToken` variables with the appropriate values for your Spark Core. For example, the Core ID and Access token used above would change: 

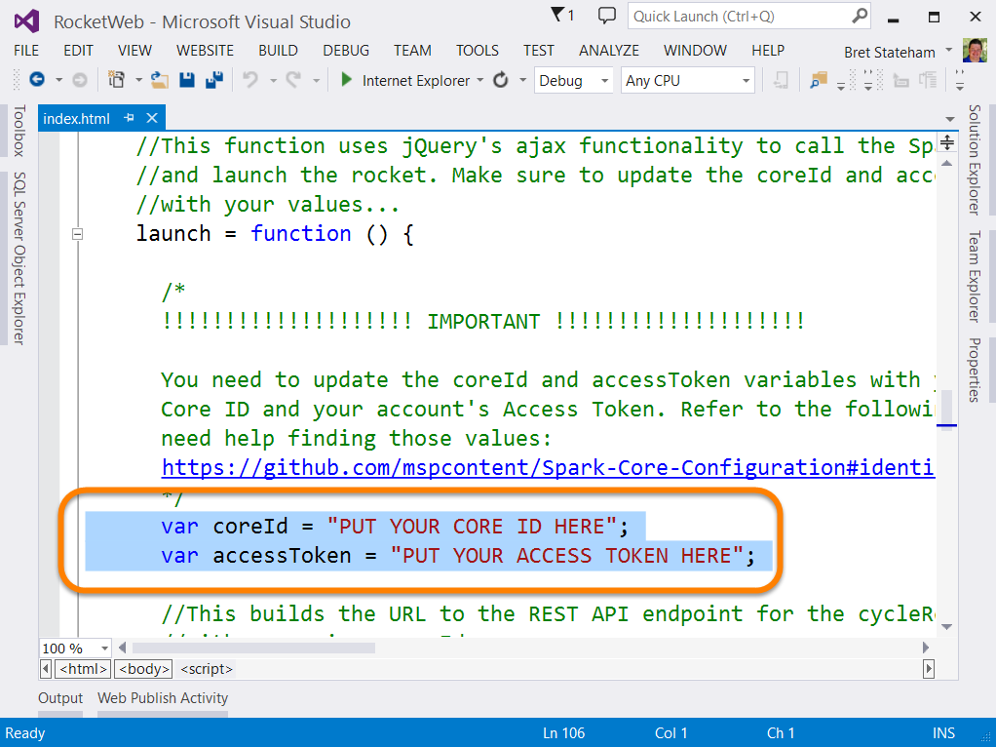
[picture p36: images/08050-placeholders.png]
08050-PlaceHolders Place Holders
	

	with

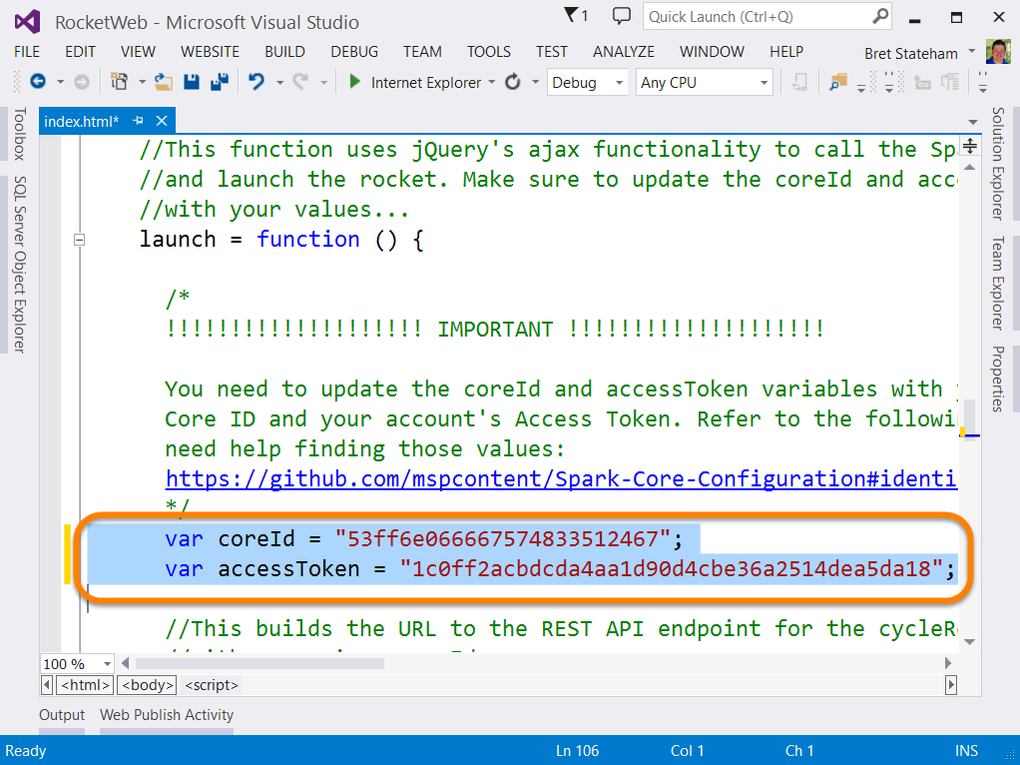
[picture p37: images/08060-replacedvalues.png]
08060-ReplacedValues Replaced Values
	

1. Now, from the Visual Studio toolbar clic the **"Save All"** button (if you are prompted for a location to save your .sln file, accept the default, or choose a path you prefer), then click the **"Debug"** button to debug the site in the browser:

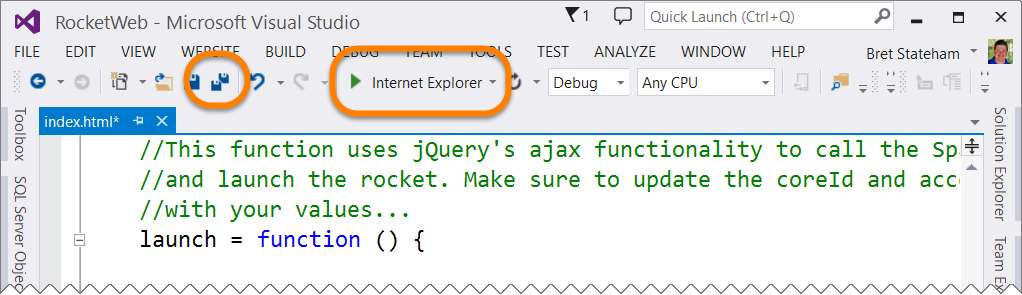
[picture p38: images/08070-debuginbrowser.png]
08070-DebugInBrowser Debug In Browser
	

1. The page should open in the browser:

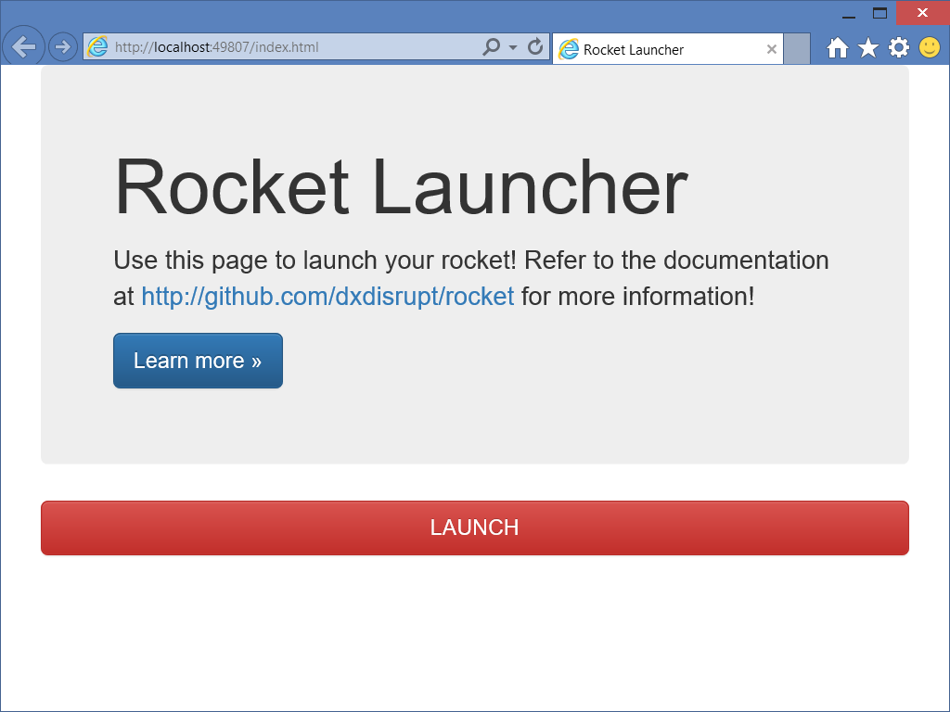
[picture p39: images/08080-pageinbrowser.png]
08080-PageInBrowser Page in Browser
	

1. Before launching, make sure that:

	- you properly updated the `coreId` and `accessToken` variables as just described
	- your spark core is powered on and breathing cyan
	- you may NOT want the rocket actually on the launcher, you can verify that the site is working just by viewing the LEDs on the relay board.  It is up to you.

1. When you are ready, click the **"LAUNCH"** button, and verify that the info message is displayed:

	> **Note:** Watch the LED above your relay on the relay board to verify that it is activating.  Of course, if you had the launcher charged, and a rocket ready to launch, it should have launched now.  

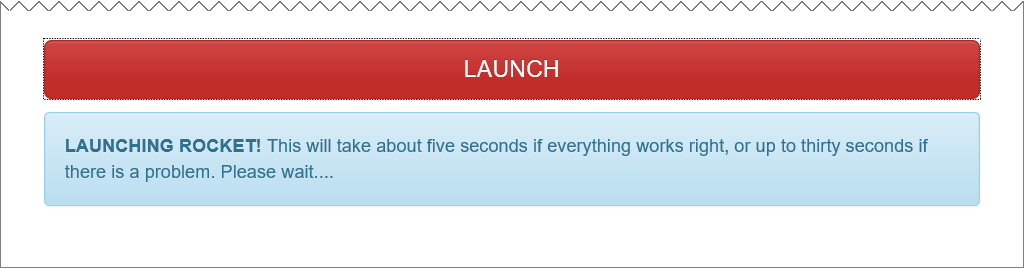
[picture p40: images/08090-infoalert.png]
08090-InfoAlert Info Alert
	

1. Assuming everything worked, the success alert message should be shown:

	08100-SuccessAlert Success Alert

1. Or if there were any problems, the failure alert will display:

	- Verify the `coreId` and `accessToken` variable values
	- Ensure that the Spark Core is powered on and breathing cyan
	- Ensure that you properly flashed the relayWidget app to the Spark Core

	08110-FailureAlert Failure Alert

---

<a name="Task9" />
## Publishing your Web Site to Azure ##

Cool, we are now launching the rocket from a web page, but it the page is running on our local development workstation.  If we'd like to be able to use that web page to fire the rocket from mobile device, or from anywhere else in the world, we need to get the web site up where people can access it from the Internet.  One of the easiest ways to do that is with an Azure Web Site.  

> **Note:** In order to do this task, you will need a current, valid Azure subscription.  If you don't have one, you can create a free trial account at http://azure.microsoft.com 

1. Ensure that the web site is open in Visual Studio

1. In the **"Solution Explorer"** window, right click on the name of your web site, and select **"Publis Web Site"** from the pop-up menu:

	09010-PublishWebSiteMenu Publish Web Site Menu Item

1. In the **"Publish Web"** window, select **"Microsoft Azure Web Sites"**:

	09020-SelectAzureWebSites Select Azure Web Sites

1. If you aren't already signed into your Azure account, click the **"Sign In..."** button, and when prompted, enter the credentials associated with the Azure subscription you want to use:

	09030-SignInIfNeeded Sign In if Needed

1. Once you are signed in, click the **"New..."** button to create a new Azure Web Site (or if you have already created the site you want to deploy to, you can select it from the drop-down list):

	09040-NewButton New Button

1. In the **"Create site on Microsoft Azure"** window, complete the fields, and click **"Create"**

	- **Site name** must be a unique host name.
	- **Subscription** should be the subscription you want to use
	- **Region** should be a region near you
	- **Database server** should be **No database** (this site doesn't use one)

	09050-CreateNewWebSite Create New Web Site

1. On the **Publish Web"** page, accept the defaults (Visual Studio got these straight from Azure, so they should be correct), and click the **"Publish"** button:

	09060-Publish Publish

1. Back in Visual Studio, you can monitor your publish progress in the **"Output"** and **"Web Publish Activity"** windows:

	09070-OutputWindow Output Window

	09080-WebPublishActivity Web Publish Activity Window

1. As long as the publish process completes successfully though, your new Azure Web Site should open in the browser:

	09090-SiteInAzure Site in Azure

1.  You should now be able to open that site from anywhere, and use it to launch your rocket! So cool! For example, here it is running on a Windows Phone:

	09100-OnWindowsPhone On Windows Phone!

---

<a name="summary" />
## Summary ##

The Compressed Air Rocket Launcher and Spark Core is a great way to engage kids, friends, family, and even large audiences.  Everybody loves to see the rocket launch, and the construction, electronics and code are actually all pretty simple!  

Have fun!

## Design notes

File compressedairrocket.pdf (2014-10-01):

# COMPRESSED AIR ROCKET

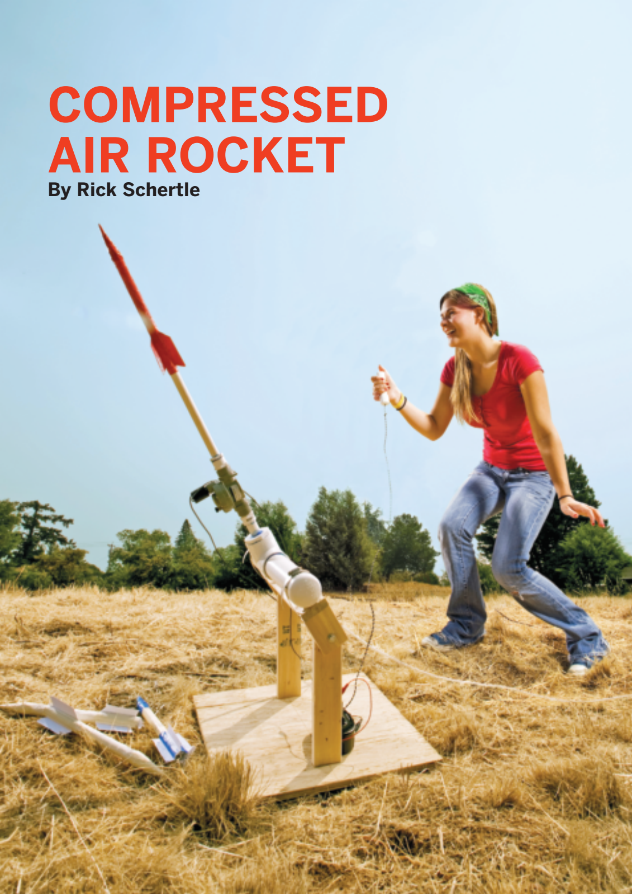
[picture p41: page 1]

102 Make: Volume 15

PROJECTS: AIR ROCKET | makezine.com/15/airrocket

# By Rick Schertle

Make: 103

Photograph by Gabriela Hasbun

Rick Schertle (schertle@yahoo.com) is a master at the craft of teaching middle school in San Jose and a novice maker at home. His diverse interests include backyard chickens, adventure travel, veggie oil-fueled cars, and geocaching — all made more fun with the enthusiastic support of his wife and the crazy antics of his young son and daughter.

Set up: p.105 | Use it: p.113

PAPER, TAPE,

# COMPRESSED AIR … LIFT-OFF!

# Blow your friends away as you send this

25-cent rocket hundreds of feet in the air.

# You can build this easy launcher and rocket with common hardware store

items in an afternoon.

## All the parts for this simple but impressive air rocket and launcher are cheap and easy to find. Building it is a breeze

and the modifications are endless. It’s legal in a big city,

## reusable, clean, and can be launched even in high winds

on a small field.

## Believe me, folks are quite taken by the 200- to 300-foot

flights fueled by 18 or so bicycle pumps of compressed air.

## Whether you’re launching on your own or with a whole

group of rocketeers, watch the crowds gather … 3, 2, 1,

## and away!

# Make it: p.106

CAUTION: DANGEROUS PROJECT
At normal temperatures, standard Schedule 40 PVC has a working pressure of around 150psi, but heat, sunlight, solvents, scratches, and time make the material lose strength, and even at the 75psi used for this project, it will eventually fail. When it fails, it will break into fragments that can be thrown with great force by the compressed air. For added safety, wear safety goggles and wrap PVC elements in several layers of duct tape (not shown) to minimize any possible shrapnel. For a bomb-proof model, you could also build the entire system out of galvanized steel pipe at a greater expense.

!

# PUMP IT UP, UP, AND AWAY!

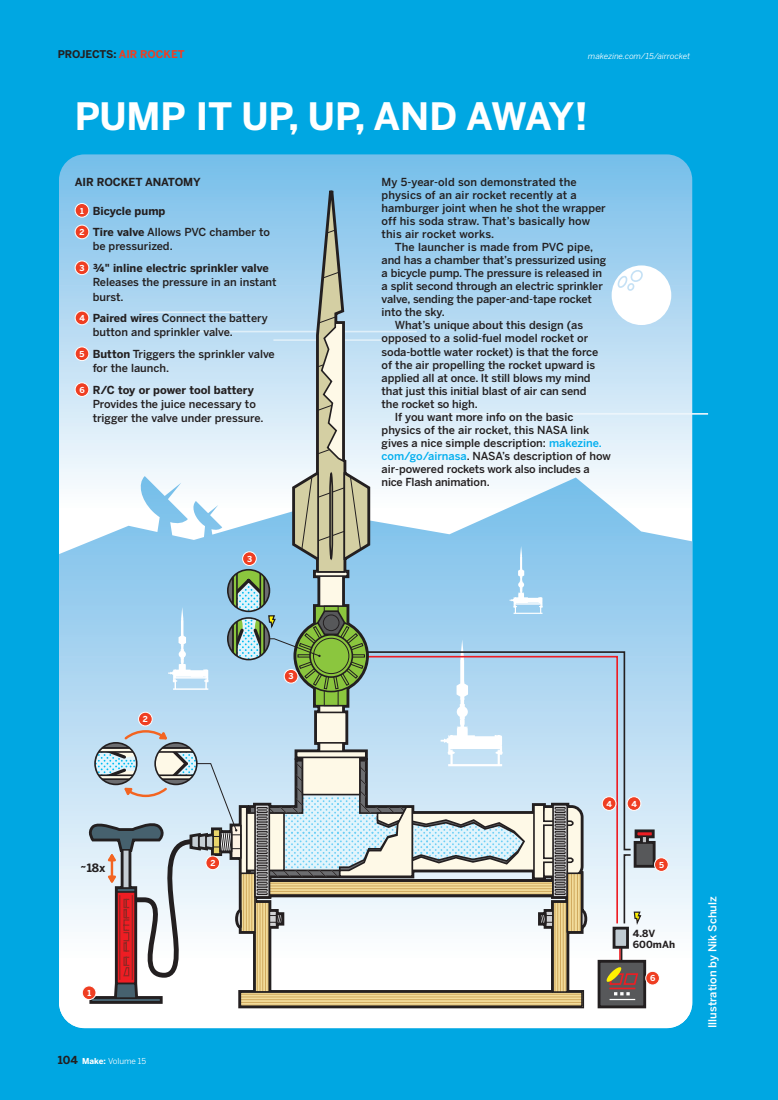
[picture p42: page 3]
104 Make: Volume 15; 4.8V 600mAh

AIR ROCKET ANATOMY

My 5-year-old son demonstrated the
physics of an air rocket recently at a
hamburger joint when he shot the wrapper
off his soda straw. That’s basically how
this air rocket works.
The launcher is made from PVC pipe,
and has a chamber that’s pressurized using
a bicycle pump. The pressure is released in
a split second through an electric sprinkler
valve, sending the paper-and-tape rocket
into the sky.
What’s unique about this design (as
opposed to a solid-fuel model rocket or
soda-bottle water rocket) is that the force
of the air propelling the rocket upward is
applied all at once. It still blows my mind
that just this initial blast of air can send
the rocket so high.
If you want more info on the basic
physics of the air rocket, this NASA link
gives a nice simple description: makezine.
com/go/airnasa. NASA’s description of how
air-powered rockets work also includes a
nice Flash animation.

1 Bicycle pump
2 Tire valve Allows PVC chamber to
be pressurized.
3 ¾" inline electric sprinkler valve
Releases the pressure in an instant
burst.
4 Paired wires Connect the battery
button and sprinkler valve.
5 Button Triggers the sprinkler valve
for the launch.
6 R/C toy or power tool battery
Provides the juice necessary to
trigger the valve under pressure.

Illustration by Nik Schulz

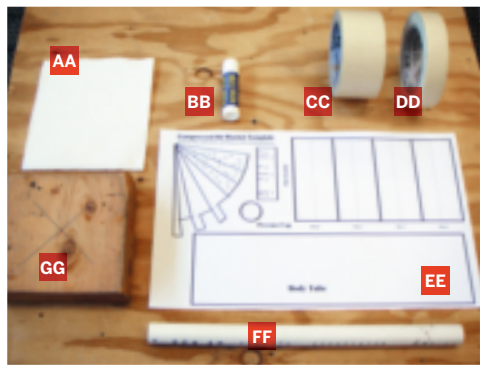
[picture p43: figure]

Make: 105

SET UP.

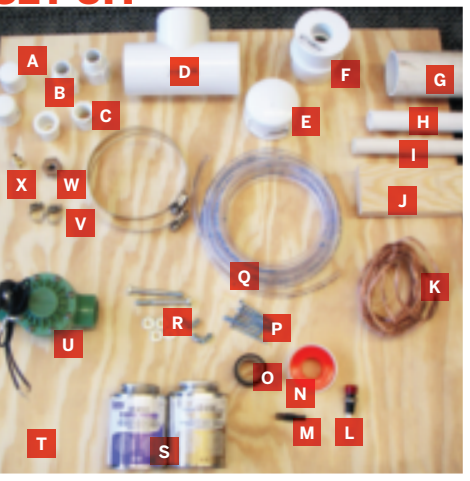
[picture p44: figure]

## MATERIALS

[A] ¾" PVC slip end caps
(2) see below

[B] ¾" PVC adapters,
¾" male threaded ×
¾" female slip (2)

[C] ¾" PVC reducers:
¾" male slip × ½" female
threaded and ½" female
slip × ¾" male slip

[D] 2" PVC slip tee

[E] 2" PVC slip end cap

[F] 2" PVC reducer bushings, male slip × ¾" female slip (2)

[G] 2" PVC pipe, 10" length

[H] ¾" PVC pipe, 3" and
4" lengths

[I] ½" PVC pipe, 16" length for launch tube

[J] 48" length of 1×3 pine board to be cut to various sizes for the launch tower

[K] 10' length of paired
wire I used speaker wire.

[L] Button momentary
switch RadioShack part
#275-609

[M] Tire air valve

[N] Teflon tape

[O] Electrical tape

[P] Wood screws, size
#6×1½" or similar (8)

[Q] 10' length of 7"
(outside diameter) × 6"
(inside diameter) flexible vinyl tubing

[R] ¼" hex bolts, 2"
long (2), wing nuts (2),
and washers (4)

[S] PVC cement and primer

[T] 24"×24" piece of
½" plywood as a base for
the launch tower

[U] ¾" inline 24V electric sprinkler valve Cheap is
fine, just make sure you
get an inline one.

[V] Hose clamps: size #4,
8"–0" (2) and size #72,
3½"–5" (2)

[W] ½" male threaded ×
1" female threaded brass
reducer bushing

[X] 6" hose barb × 1"
male threaded brass fitting

[NOT SHOWN]
Battery connector
Connectors can be the
standard R/C toy type
used for rechargeable
batteries, or a generic
bullet type.

Power tool or R/C toy
battery to trigger the sprinkler valve. Under pressure, the valve requires higher
amperage: a power tool or
R/C toy battery will work, minimum 4.8V, 600mAh.

Bicycle pump and pressure
gauge Use a pump with a
built-in gauge, or just use an ordinary pen-type tire
pressure gauge.

ROCKET BUILDING
MATERIALS
[AA] Paper napkin

[BB] Glue stick

[CC] 2"-wide masking tape

[DD] ¾"-wide masking
tape

[EE] Printed rocket
template Download it
from makezine.com/15/
airrocket and print on
8½"×14" paper.

[FF] 13" length of ½" PVC
pipe for rocket-building
stand

[GG] 5½" length of
scrap 2×6 lumber

## TOOLS

[NOT SHOWN]
Hacksaw or PVC cutter
A cheap PVC cutter is a
super handy tool for cutting hose, PVC pipe, etc.

Fine sandpaper

Rubber mallet

Utility knife

Screwdrivers

Drill and bits: r", ¼",
½", q"

Saw for cutting lumber
to various sizes

Soldering iron and solder
(optional)

Socket set (optional)

Scissors

Wire cutters

Adjustable wrench

Channel-lock pliers

Large C-clamp

Photography by Rick Schertle

Please note: Only
Schedule 40 PVC
should be used.

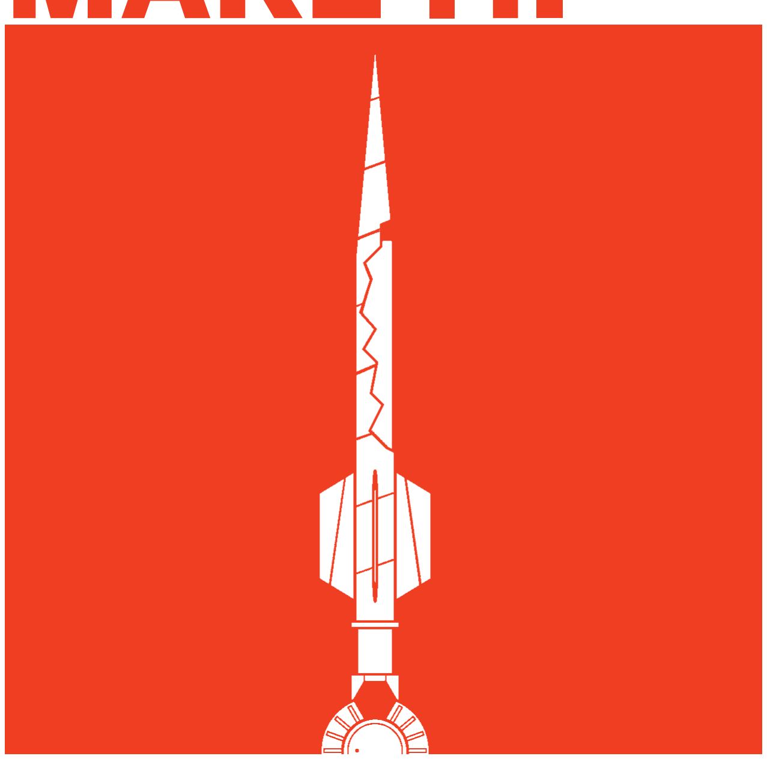
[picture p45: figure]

106 Make: Volume 15

# BUILD YOUR AIR ROCKET LAUNCHER AND ROCKETS

## START>>

MAKE IT.

## 1. ASSEMBLE THE PRESSURE CHAMBER

## Time: An Afternoon Complexity: Easy

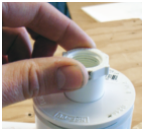
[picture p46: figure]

1a. Use PVC primer, then cement,
to glue the 2" male slip × ¾" female slip PVC reducer bushing into the 2" slip tee. Next, prime and glue the ¾" male slip × ½" female threaded PVC reducer into the 2" male slip × ¾" female slip PVC reducer bushing.

1b. Apply teflon tape to the threads of both brass fittings. Screw the brass barbed fitting to the brass ½"×1" reducer bushing. Screw the ½"×1" brass reducer bushing into the ¾" male slip × ½" female threaded PVC reducer. Tighten all connections with an adjustable wrench.

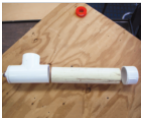
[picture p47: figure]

1c. To complete the pressure chamber assembly, prime and glue the 2" end cap onto the 10" length of 2" PVC pipe. Next, glue the 10" piece of 2" pipe into the other end of the 2" tee as shown.

Make: 107

## 2. BUILD THE LAUNCH SYSTEM

2a. Wrap teflon tape around each
of the ¾" male threaded × ¾" female slip PVC adapters. Thread the adapters onto the ¾" inline 24V electric sprinkler valve and tighten with channel-lock pliers.

2b. Cut a 3" length of ¾" PVC and a 16" length of ½" PVC. Glue the 3" piece into the “In” side of the sprinkler valve. Glue the ¾" male slip × ½" female slip reducer and the 16" length of ½" PVC into the “Out” side of the valve.

2c. Glue the 2" male slip × ¾" female slip PVC reducer bushing into the tee on the pressure chamber.

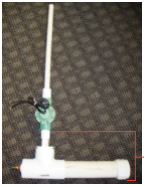
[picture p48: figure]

WARNING: Wrap
the pressure chamber with
several layers of duct tape (not shown) to prevent
injury in case the chamber shatters under pressure.

2d. Glue the completed launch assembly into the pressure chamber. Your air launch system is complete.

!

108 Make: Volume 15

## 3. BUILD THE LAUNCH TOWER AND ATTACH THE LAUNCH SYSTEM

3a. Cut your ¾"×3" lumber to the following lengths: 15" (1), 3½" (2), and 12" (2).

3b. Clamp a 3½" length to the 15" length as shown. Pre-drill 2 holes with the r" bit and then screw in the 1½" screws using a drill/driver. A bit of wood glue would be good too, if available. Repeat with the other 3½" length on
the other side.

3c. Mark a 3½" piece 1" from the
bottom, mark a 12" piece 2" from the top, line them up, and sandwich them together using a C-clamp. Drill a ¼" hole through both pieces, then slip a ¼" hex bolt through, with washers on both sides and a wing nut on the outside. Repeat on the other side.

3d. The 24"×24" piece of plywood will provide a sturdy base for the launch tower. Measure and mark a line down the center of the plywood, 12" in from either side. On your centerline, measure and mark 4½" in from both ends. Place the legs of the launch tower with their edges on the inside of the marks, then trace a line around each leg. Drill two r" holes in each traced area.

3e. Turn the whole thing upside down, line up the launch tower on the marks, and then finish drilling pilot holes into the launch tower legs, through the existing holes in the plywood. Screw into place.

3f. Once your base is secure, attach the pressure chamber/launch system to the horizontal board using the
2 large hose clamps. Your launch tower is complete.

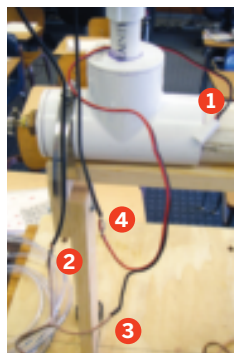
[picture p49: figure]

Make: 109

## 4. MAKE AND WIRE THE LAUNCH BUTTON

4a. Drill a ¼" hole in the middle of one ¾" PVC slip end cap, and drill a ½" hole in the middle of the other to accommodate the button switch.

4b. Thread the paired wire through the end cap with the smaller hole, from the
outside, and tie a knot about 8" from the end, so the knot is inside the cap. Now
thread the end of the wire in the following order — through the 4" piece of ¾" PVC, through the nut and washer for the button, then through the ½" hole in the other ¾" end cap, from the inside.

4c. Solder the wire ends to the leads
on the bottom of the button. Slip the washer and nut over the button, inside the PVC cap, and tighten the nut using a pair of needlenose pliers. This can be a bit tricky.

4d. Push everything together to complete the button assembly. Don’t glue it, in case you need to make repairs to your button later.

4e. Connect the wiring. Solder connections when possible, and insulate them with electrical tape.

### 1. Use bullet connectors or something similar to connect the battery leads

to the button and the electric valve.

### 2. Connect 1 wire from the button to 1 lead on the sprinkler valve. Twist, then

solder and/or tape.

### 3. Connect the other wire from the button to one of the bullet connectors

on the battery leads (red or black, it doesn’t matter).

### 4. Connect the remaining battery connector to the remaining lead on the

sprinkler valve.

4f. Tape the wire for the button to the vertical support of the launch tower. Test your launch button. When you press the button, you should hear the sprinkler valve click open and closed. You’ll do more testing later when the system is under pressure.

110 Make: Volume 15

## 5. MAKE THE AIR HOSE AND TEST THE LAUNCH SYSTEM

5a. Now we’re going to assemble and attach the air hose to the launcher. First, strip the rubber off the tire valve. You can use fine sandpaper to clean off the valve so it’s shiny.

5b. Slip the tiny hose clamp over the hose and insert the tire valve into the hose. Push it in as far as you can. Tighten the hose clamp over the tube and valve using a socket or screwdriver. This connection was the Achilles’ heel in my prototype launcher. Granted, it was exciting to have the hose explode off at 75psi, hissing wildly like a snake, but, for the sake of reliability, I’ve strengthened it by using the mini hose clamps.

Slip the second mini hose clamp over the other end of the hose, and push the hose end onto the 6" hose barb. Tighten the clamp over the hose and barb. If you find the clamp too big and you’re not able to get it really tight, wrap the
barb in rubber from a bike inner tube and then tighten the clamp over that.

5c. Attach the bicycle pump to the tire valve and pressurize the system to about 75psi. Keep an eye on the gauge and listen for any hissing. The pressure should stay at 75psi. If you find leaks, fix them and try again.

Release the pressure by pressing the launch button (with the battery connected). Be careful when you do this — wear eye protection and stand clear of the pressure chamber.

If the pressure doesn't release when you press the button, tighten down the solenoid (the black thing with the wires coming out) on the sprinkler valve. You may also need a larger battery (one with more amps) to trigger the solenoid under pressure.

If you’re still having problems with your electrical system, most valves have a manual trigger you can flip to release the pressure. If you’re up this close to the valve you may want hearing protection as well. Be very careful that your head is away from the launch tube.

## 6. BUILD THE ROCKET ASSEMBLY STAND

Mark the center of a 5½" scrap of 2×6
lumber. Drill a q" hole 1" deep in the center. This is where a drill press is really handy. Then twist a 13" length of ½" PVC pipe into the hole. Add masking tape to the base of the pipe, if needed, to get a snug fit.

Make: 111

## 7. BUILD THE ROCKETS

7a. Download the rocket template from makezine.com/15/airrocket and print it out on 8½"×14" paper. Cut out all the pieces on the solid lines as shown.

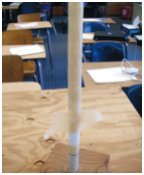
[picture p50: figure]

7b. Wrap the body tube around the assembly stand and tape it in 5 places with the ¾" masking tape. The smoother your tape, the more aerodynamic your rocket will be. Now wrap the body tube with 2" masking tape, working your way down. Slide the body tube to the top of the PVC stand. Tape the pressure cap on top of the body tube by crisscrossing ¾" tape over the top, and smooth it down.
NOTE: Make sure to
overlap the tape, making
it about 2 layers thick
everywhere. If you miss
a spot, you’ll have a
dramatic blowout!

7c. Curl the nose cone around to overlap the dotted section, and tape it in place. Stuff the nose cone tightly with the napkin. A full napkin should fit in. Use a pencil to pack it tightly.

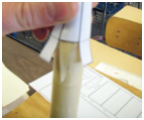
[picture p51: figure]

7d. Place the nose cone on top of the body tube, tape around the tabs, then cover the nose cone in tape.

112 Make: Volume 15

7h. Line up the fins with the marks on the bottom of the body tube. Tape all fins securely in place.

Your rocket is now complete and ready to launch. The great thing about these rockets is that no matter how they’re built, they will fly! Some of course will fly better than others, but they all will fly to some degree.

## FINISH X

NOW GO USE IT »

7e. Wrap the fin guide around the PVC pipe at the base of the body tube and mark on the 3s for a 3-fin model or the 4s for 4 fins.

7f. Fold the fins on the dashed lines, then stack them together and trim the tops and bottoms at an angle.

7g. Glue the fins together with a glue stick, and pinch them to adhere them. Make sure you don’t glue the tabs that will be used to attach the fins to the rocket.

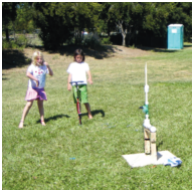
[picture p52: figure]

Make: 113

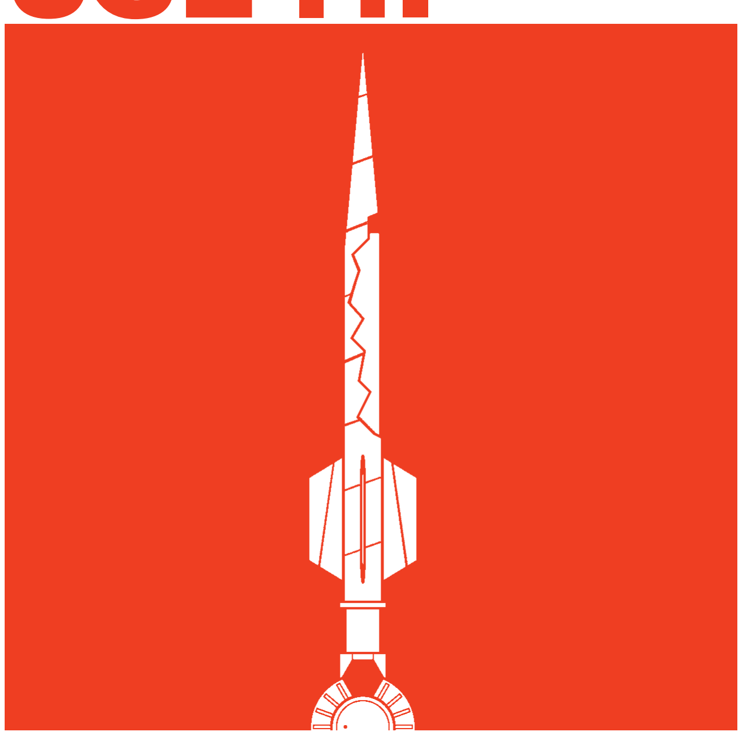
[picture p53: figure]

ROCKET SAFETY,
SITE SELECTION,
OPERATION,

# AND CONTESTS

USE IT.

## SAFETY

As with any air-powered device, you have to use caution. Eye injuries are your biggest danger. Safety goggles for you and any spectators are required.

## SITE SELECTION

Because these air rockets have no recovery system, you can launch them in a fairly small area even with wind. They will go very high but then come right back down.
A small field would be an ideal launch site. The rockets are light and soft, so while it’s not ideal for them to land on cars, the chance of damage
is slight.

## OPERATION

Set the launcher on the ground and lay out the air hose and launch button wire away from the launcher.
Slide the rocket down the launch tube until it stops at the pressure cap. This is a tight fit and you may need to smooth down the inside bottom of the rocket with your fingers to get it on. You may also bevel the top of the PVC launch tube with a file to make it easier.
Connect the air pump to the hose and pump up to about 75psi. If you go above 75psi, you may blow out the side of your rocket.
Count down and then launch! With a good launch, the rocket will go nearly out of sight and then free-fall to the ground.
The rocket will get crumpled as it hits the ground, but can simply be pinched back into shape and launched again and again.
If for some reason it does not launch, follow the pressure testing instructions in Step 5c.

## CONTESTS

» Tilt the launch tower, then place a trash can 100yds away and see who can get the closest.

» Build a simple clinometer (wikihow.com/Make-a-Clinometer) and have contests to see whose rocket can get the highest.

## OTHER RESOURCES

If this MAKE project really grabs you, here’s a great article on air rockets and some more sophisticated setups, by two professors at Southern Illinois University: makezine.com/go/airrocket.

CAUTION: When placing the rocket on the launcher, make sure your head is never over the launch tube. Wear safety goggles. Make sure everyone is clear from the area before launching, and do a countdown once everyone is at a safe distance.

!

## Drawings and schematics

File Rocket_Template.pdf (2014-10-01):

## Compressed Air Rocket Template

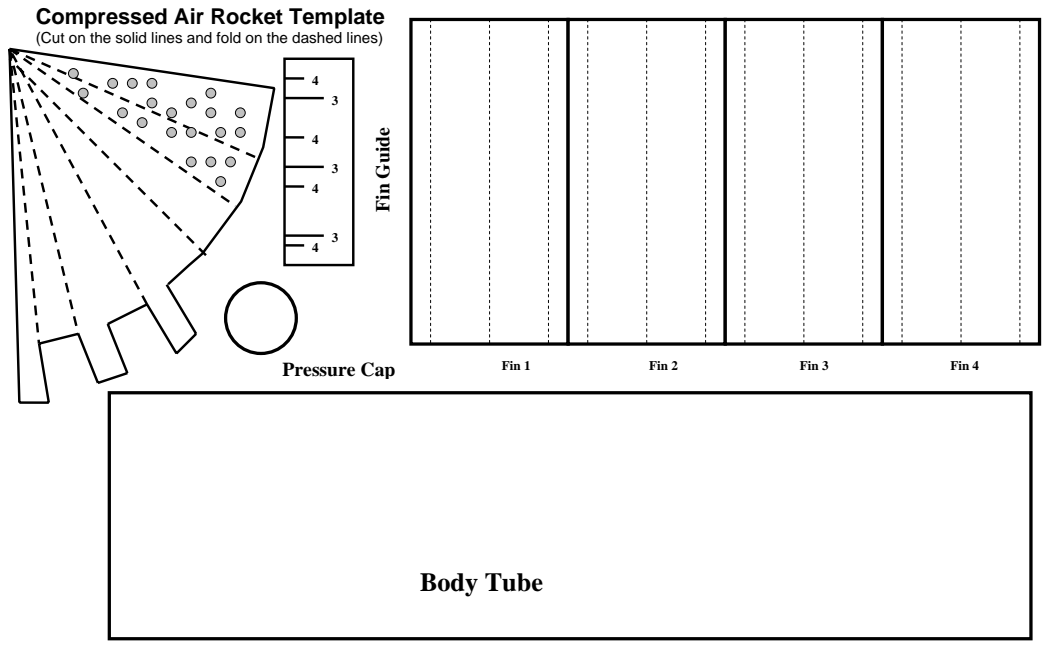
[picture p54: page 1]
Body Tube; Pressure Cap; Fin Guide; Fin 1; Fin 2; Fin 3; Fin 4

(Cut on the solid lines and fold on the dashed lines)
